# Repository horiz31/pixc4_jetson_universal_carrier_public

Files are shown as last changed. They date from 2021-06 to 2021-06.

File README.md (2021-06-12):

# PixC4 Jetson Universal Carrier Board Design Template
Schematic and Kicad board design for a PixC4-Jetson Universal Carrier Board

This project is intended to help users design a custom carrier board for the PixC4-Jetson. It contains a verified working design providing wide-input DC power regulation and typical connector pinouts.

A STEP file with 3D models is available here: https://drive.google.com/file/d/1p-Tw4490VoOuMsqg2tXlwOgqGBfQfWUK/view?usp=sharing

Designed in KiCad 5.1.8. KiCad is available for free download: https://www.kicad.org/download/

## Design Notes
#### Power
Power regulation is handled by two TI TPS54561QDPRRQ1 dc-dc converters. One is used to power the +5V bus, which is used to power the Nvidia Jetson. The other is used to power the +5V_FMU bus which is used to power the FMU. In general it is good design practice to separate the power system between that used for the Jetson and the FMU as we have done in this design. This way, even if an issue causes the Jetson bus to go into over-current protection, the core FMU may remain functional.

It is possible to implement a Power Selection Unit (PSU) for the FMU, providing even further redundancy. The ~VDD_POWERA_VALID and ~VDD_POWERB_VALID lines can be used in conjunction with a PSU to inform the FMU about the active power source. Note that the FMU USB port on the PixC4-Jetson can also power the FMU system, as this is useful for setup and downloading log files.

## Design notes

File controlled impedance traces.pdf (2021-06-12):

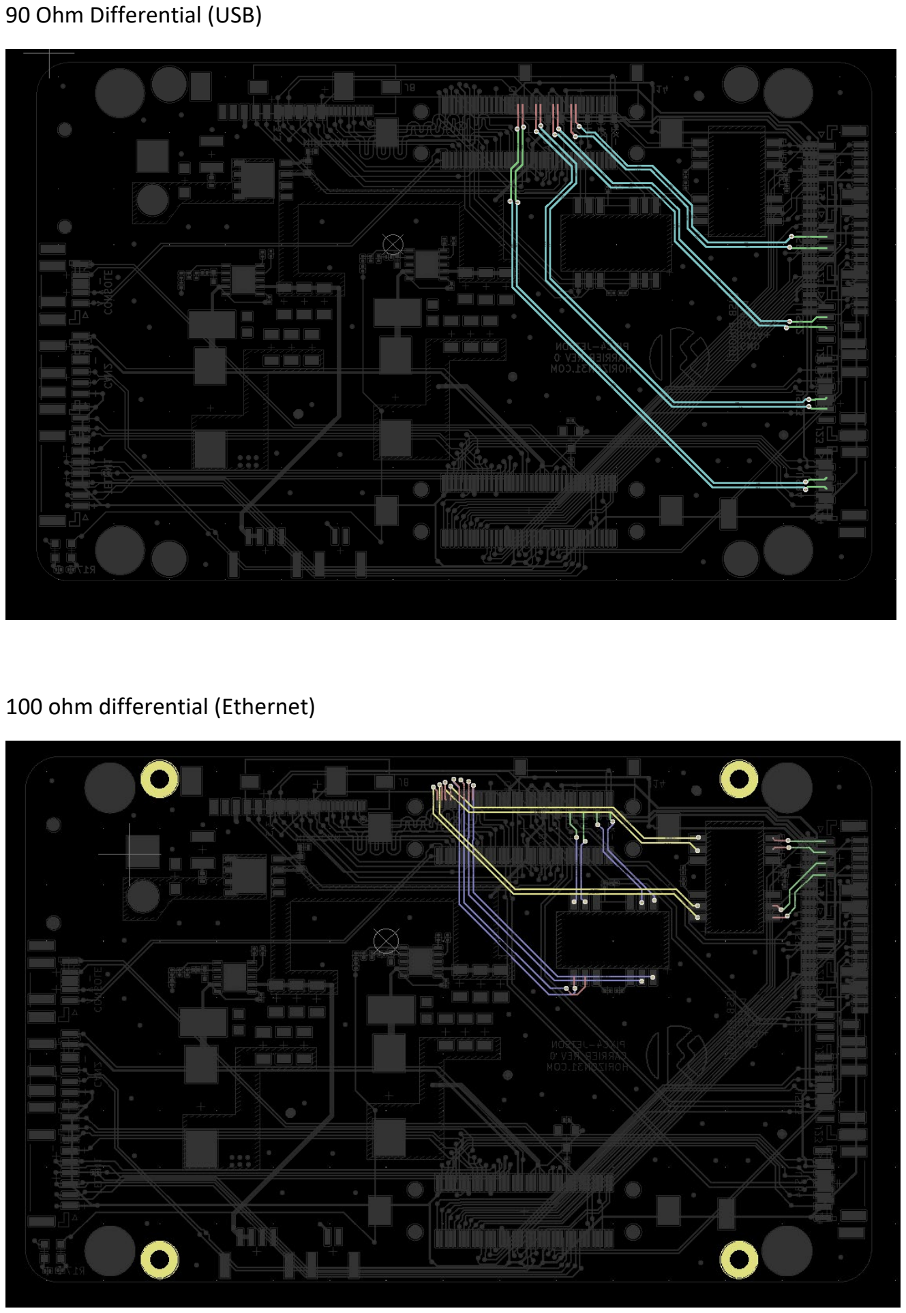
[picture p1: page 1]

90 Ohm Differential (USB)

100 ohm differential (Ethernet)

95 ohm differential (MIPI)

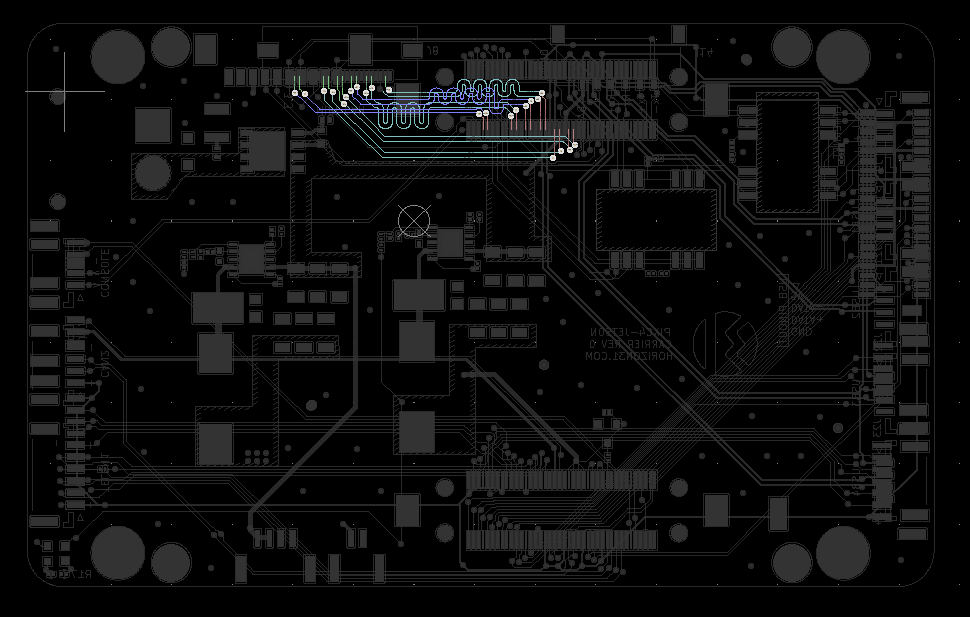
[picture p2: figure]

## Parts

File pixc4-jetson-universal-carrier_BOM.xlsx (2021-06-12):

PixC4-Jetson Universal Carrier Rev 1
Item | Qty | Reference(s) | Value | LibPart | Footprint | Part Num | Notes
1 | 6 | C1, C2, C3, C4, C20, C21 | 0.1uF | Device:C | Capacitors_SMD:C_0201 | GRM033R61E104KE14J
2 | 2 | C5, C6 | 1000pF | Device:C | Capacitors_SMD:C_0201 | GRM033R71H102KA12D
3 | 6 | C7, C8, C10, C11, C12, C13 | 2.2uF 100V | Device:C | Capacitors_SMD:C_1206 | 12061C225KAT2A
4 | 1 | C9 | 10uF 100V | Device:C | Capacitors_SMD:C_1210 | GRM32EC72A106KE05L
5 | 2 | C14, C15 | 10nF | Device:C | Capacitors_SMD:C_0201 | GRM033R71E103KE14D
6 | 2 | C16, C17 | 4.7nF | Device:C | Capacitors_SMD:C_0201 | GRM033R61E472KA12D
7 | 2 | C18, C19 | 47pF | Device:C | Capacitors_SMD:C_0402 | C0402C470J3RACAUTO
8 | 6 | C22, C23, C24, C25, C26, C27 | 47uF 10V | Device:C | Capacitors_SMD:C_1206 | CL31A476MPHNNNE
9 | 1 | D1 | TVS | osrf_device_fork:TVS | Diodes_SMD:D_SOD-123F | ATV02W101B-HF
10 | 2 | D2, D3 | PDS760-13 | Device:D_Schottky | UVDL:PDS760-13 | PDS760-13
11 | 2 | D4, D5 | LED_G | Device:LED | LEDs:LED_0603 | 150060VS75000
12 | 1 | D6 | D_Zener | Device:D_Zener | Diodes_SMD:D_SOD-523 | MM5Z12VT1G
13 | 6 | FID1, FID2, FID3, FID4, FID5, FID6 | Fiducial | Mechanical:Fiducial | Fiducials:Fiducial_0.5mm_Dia_1mm_Outer | DNI | DNI
14 | 4 | J1, J2, J3, J4 | Conn_01x01 | Connector_Generic:Conn_01x01 | Mounting_Holes:MountingHole_2.7mm_M2.5_Pad_Via | DNI | DNI
15 | 2 | J5, J6 | FX23L-80P-0.5SV10 | fx23l-80p-0.5sv8:FX23L-80P-0.5SV8 | UVDL:Hirose-FX23L-80P-0.5SV8-MFG | FX23L-80P-0.5SV10
16 | 3 | J7, J13, J16 | Conn_01x03 | Connector_Generic:Conn_01x03 | Connectors_JST:JST_GH_SM03B-GHS-TB_03x1.25mm_Angled | SM03B-GHS-TB(LF)(SN)
17 | 1 | J8 | Conn_01x22 | Connector_Generic:Conn_01x22 | UVDL:505110-2291 | 505110-2291
18 | 7 | J9, J12, J17, J21, J22, J23, J24 | Conn_01x04 | Connector_Generic:Conn_01x04 | Connectors_JST:JST_GH_SM04B-GHS-TB_04x1.25mm_Angled | SM04B-GHS-TB(LF)(SN)
19 | 1 | J10 | 532617010 | Connector_Generic:Conn_01x10 | Connectors_Molex:Molex_PicoBlade_53261-1071_10x1.25mm_Angled | 532617010
20 | 1 | J11 | Conn_01x02 | Connector_Generic:Conn_01x02 | Connectors_JST:JST_GH_SM02B-GHS-TB_02x1.25mm_Angled | SM02B-GHS-TB(LF)(SN)
21 | 1 | J14 | 504050-0691 | Connector_Generic:Conn_01x06 | UVDL:Molex-504050-0691-0-0-MFG | 504050-0691
22 | 1 | J15 | 5015714007 | Connector_Generic:Conn_02x20_Odd_Even | UVDL:5015714007 | 5015714007
23 | 1 | J18 | Conn_01x06 | Connector_Generic:Conn_01x06 | Connectors_JST:JST_GH_SM06B-GHS-TB_06x1.25mm_Angled | SM06B-GHS-TB(LF)(SN)
24 | 1 | J19 | Conn_01x05 | Connector_Generic:Conn_01x05 | Connectors_JST:JST_GH_SM05B-GHS-TB_05x1.25mm_Angled | SM05B-GHS-TB(LF)(SN)
25 | 1 | J20 | Conn_01x10 | Connector_Generic:Conn_01x10 | Connectors_JST:JST_GH_SM10B-GHS-TB_10x1.25mm_Angled | SM10B-GHS-TB(LF)(SN)
26 | 1 | J25 | Conn_01x07 | Connector_Generic:Conn_01x07 | Connectors_JST:JST_GH_SM07B-GHS-TB_07x1.25mm_Angled | SM07B-GHS-TB(LF)(SN)
27 | 1 | J27 | XT30PW-M | Connector_Generic:Conn_01x02 | UVDL:AMASS_XT30PW-M_1x02_P2.50mm_Horizontal | XT30PW-M
28 | 2 | L1, L2 | ASPIAIG-F1040-7R3M-T | Device:L | UVDL:ASPIAIG-F1040-7R3M-T | ASPIAIG-F1040-7R3M-T
29 | 1 | Q1 | Q_NMOS_GSD | Device:Q_NMOS_GSD | TO_SOT_Packages_SMD:SOT-23 | BSS214NH6327XTSA1
30 | 1 | Q2 | FDWS9508L | archangel:FDWS9508L | patrios:TRANS_FDMS0300S | FDWS9508L-F085
31 | 1 | R1 | 10K | Device:R | Resistors_SMD:R_0201 | ERJ-1GNF1002C
32 | 1 | R2 | 220 | Device:R | Resistors_SMD:R_0201 | ERJ-1GNF2200C
33 | 2 | R3, R4 | 75 | Device:R | Resistors_SMD:R_0201 | ERJ-1GNF75R0C
34 | 1 | R5 | 750m | Device:R | Resistors_SMD:R_0402 | ERJ-2BQJR75X
35 | 2 | R6, R7 | 16.9K | Device:R | Resistors_SMD:R_0201 | ERJ-1GNF1692C
36 | 2 | R8, R9 | 243K | Device:R | Resistors_SMD:R_0201 | ERJ-1GNF2433C
37 | 2 | R10, R13 | 49.9 | Device:R | Resistors_SMD:R_0201 | ERJ-1GEF49R9C
38 | 2 | R11, R14 | 53.6K | Device:R | Resistors_SMD:R_0201 | ERJ-1GNF5362C
39 | 2 | R12, R15 | 10.2K | Device:R | Resistors_SMD:R_0201 | ERJ-1GNF1022C
40 | 2 | R16, R17 | 1.0K | Device:R | Resistors_SMD:R_0201 | ERJ-1GEF1001C
41 | 1 | R18 | 10K | Device:R | Resistors_SMD:R_0402 | ERJ-PA2J103X
42 | 1 | R19 | 100 | Device:R | Resistors_SMD:R_0201 | ERJ-U01F1000C
43 | 2 | U1, U2 | HX0068ANLT | Microhard:HX0068ANLT | Nightcrawler:HX0068ANLT_r2 | HX0068ANLT
44 | 2 | U3, U4 | TPS54561QDPRRQ1 | TPS54561DPRR:TPS54561DPRR | UVDL:SON80P400X400X80-11N | TPS54561QDPRRQ1
45 | 1 | U5 | DoodleSmart | archangel:DoodleSmart | Nightcrawler:Doodle | DNI

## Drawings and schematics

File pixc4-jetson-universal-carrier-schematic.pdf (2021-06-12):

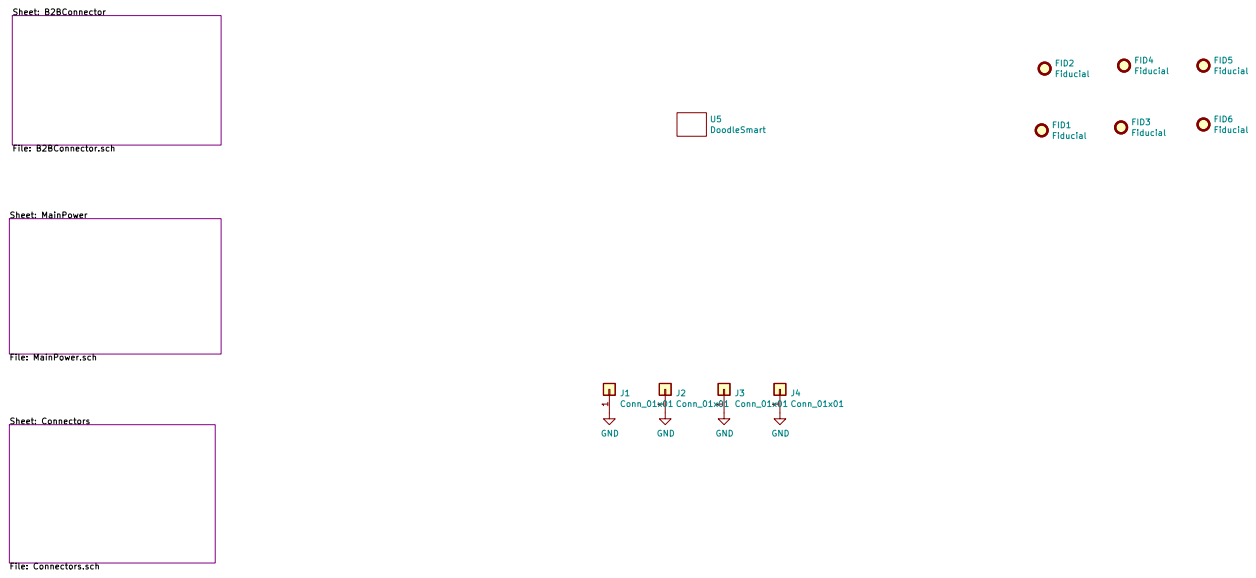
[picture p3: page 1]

Sheet: Connectors File: Connectors.sch

File: pixc4-jetson-universal-carrier.sch Sheet: / Horizon31.com

Id: 1/4 Title: PixC4-Jetson Universal Carrier

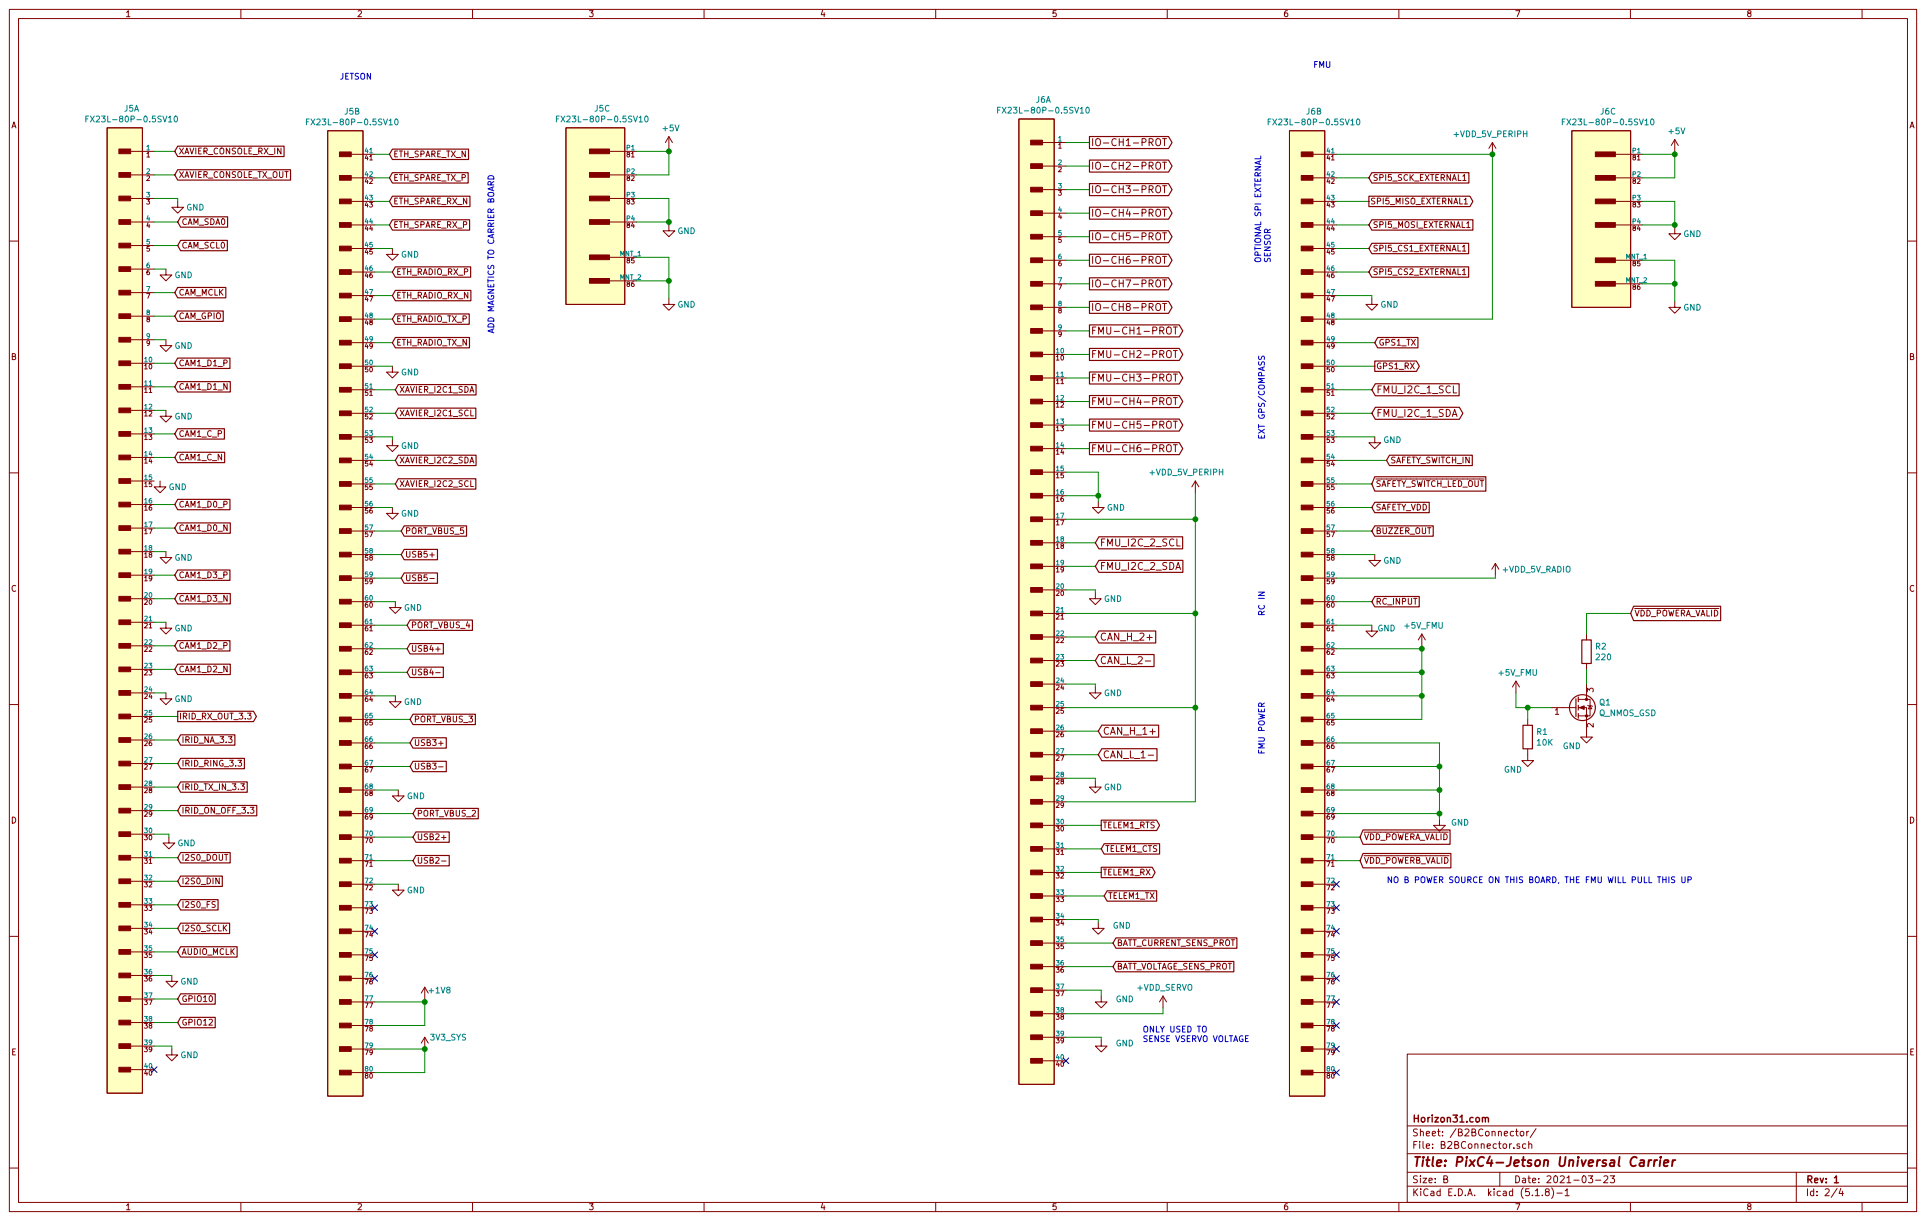
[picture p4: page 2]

GND GND GND GND GND GND GND

Id: 2/4 Title: PixC4-Jetson Universal Carrier File: B2BConnector.sch Sheet: /B2BConnector/ Horizon31.com

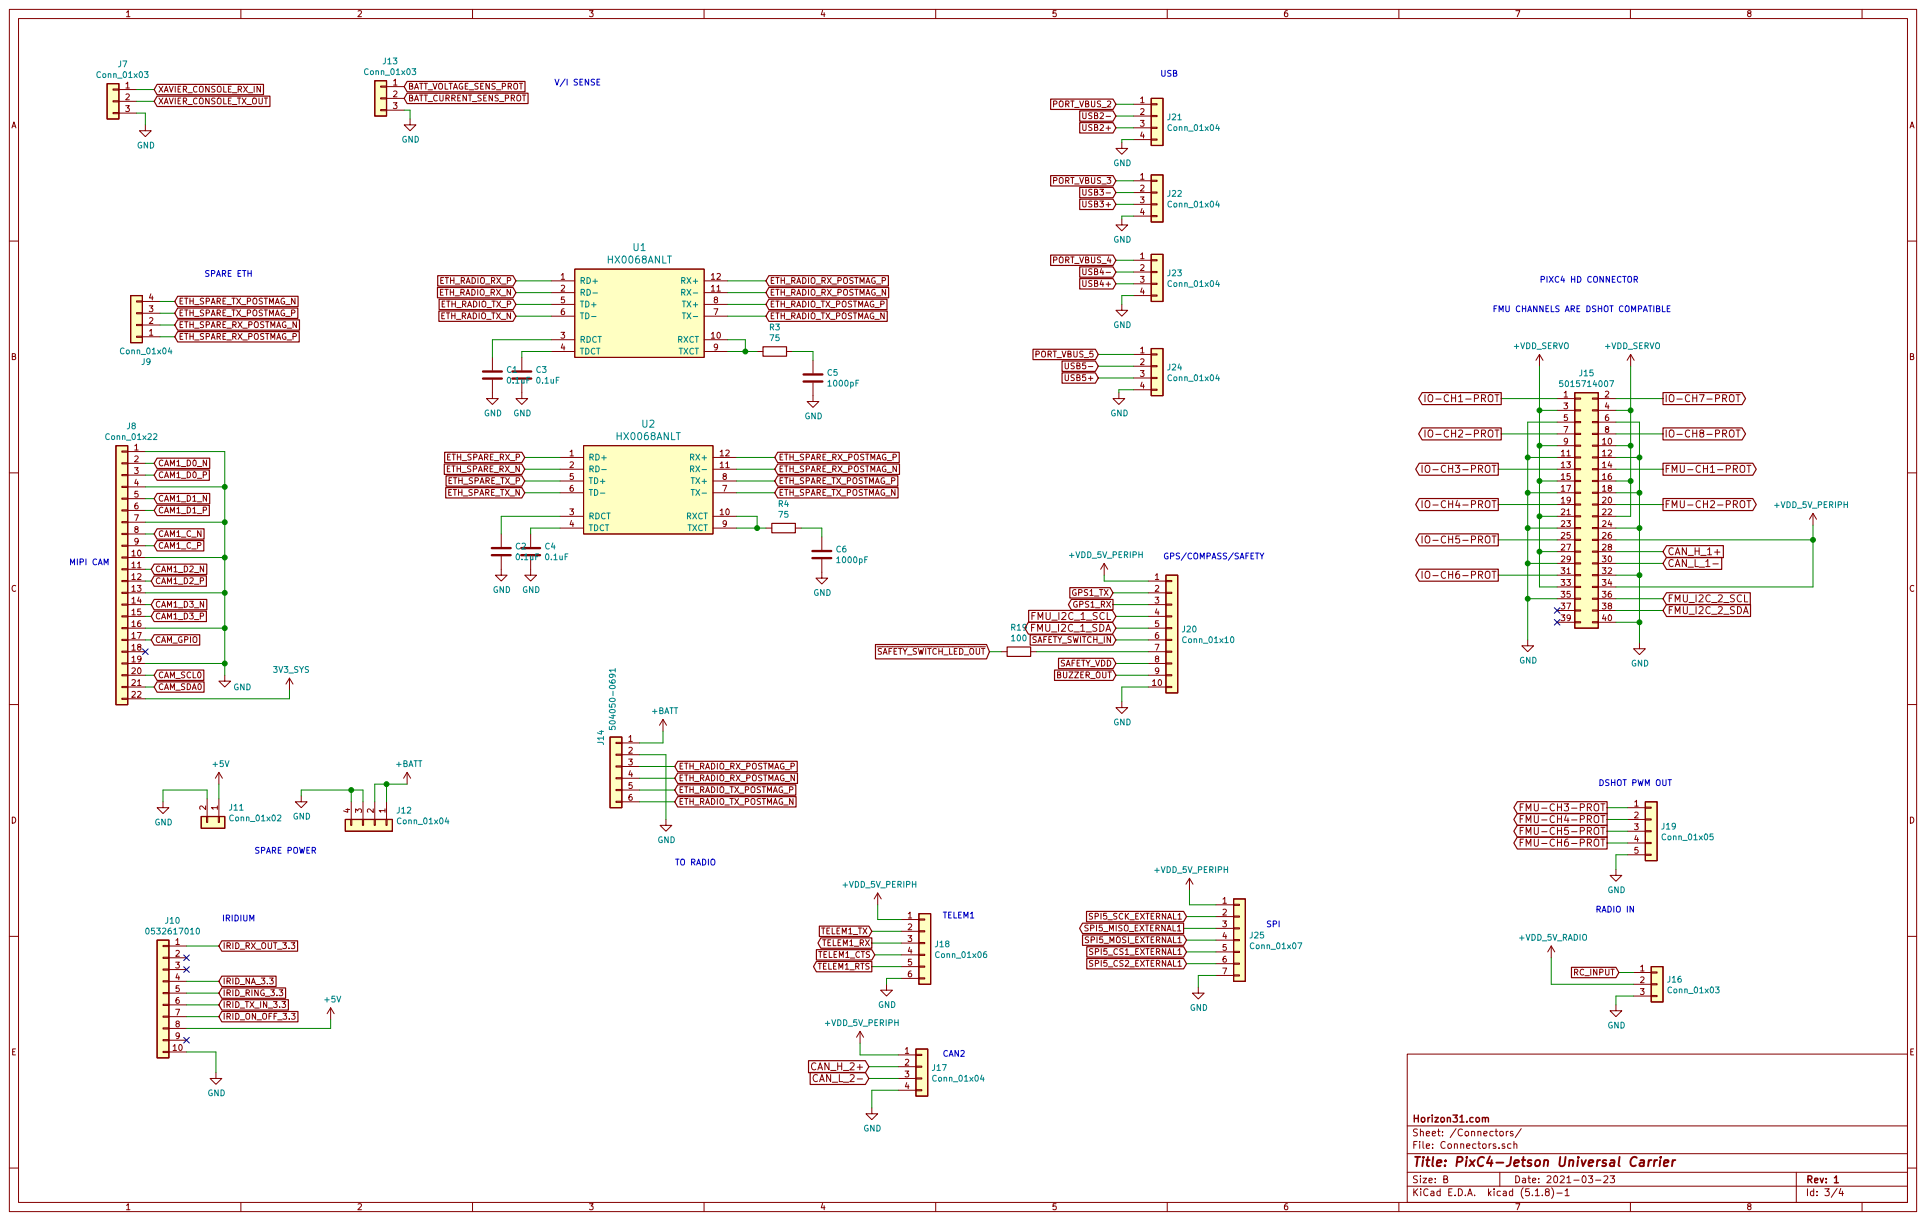
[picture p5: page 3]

FMU CHANNELS ARE DSHOT COMPATIBLE

9 | | 10
11 | | 12
13 | | 14
15 | | 16
17 | | 18
19 | | 20
21 | | 22
23 | | 24
25 | | 26
27 | | 28
29 | | 30
31 | | 32
33 | | 34

SPARE POWER MIPI CAM

Id: 3/4 Title: PixC4-Jetson Universal Carrier File: Connectors.sch Sheet: /Connectors/ Horizon31.com

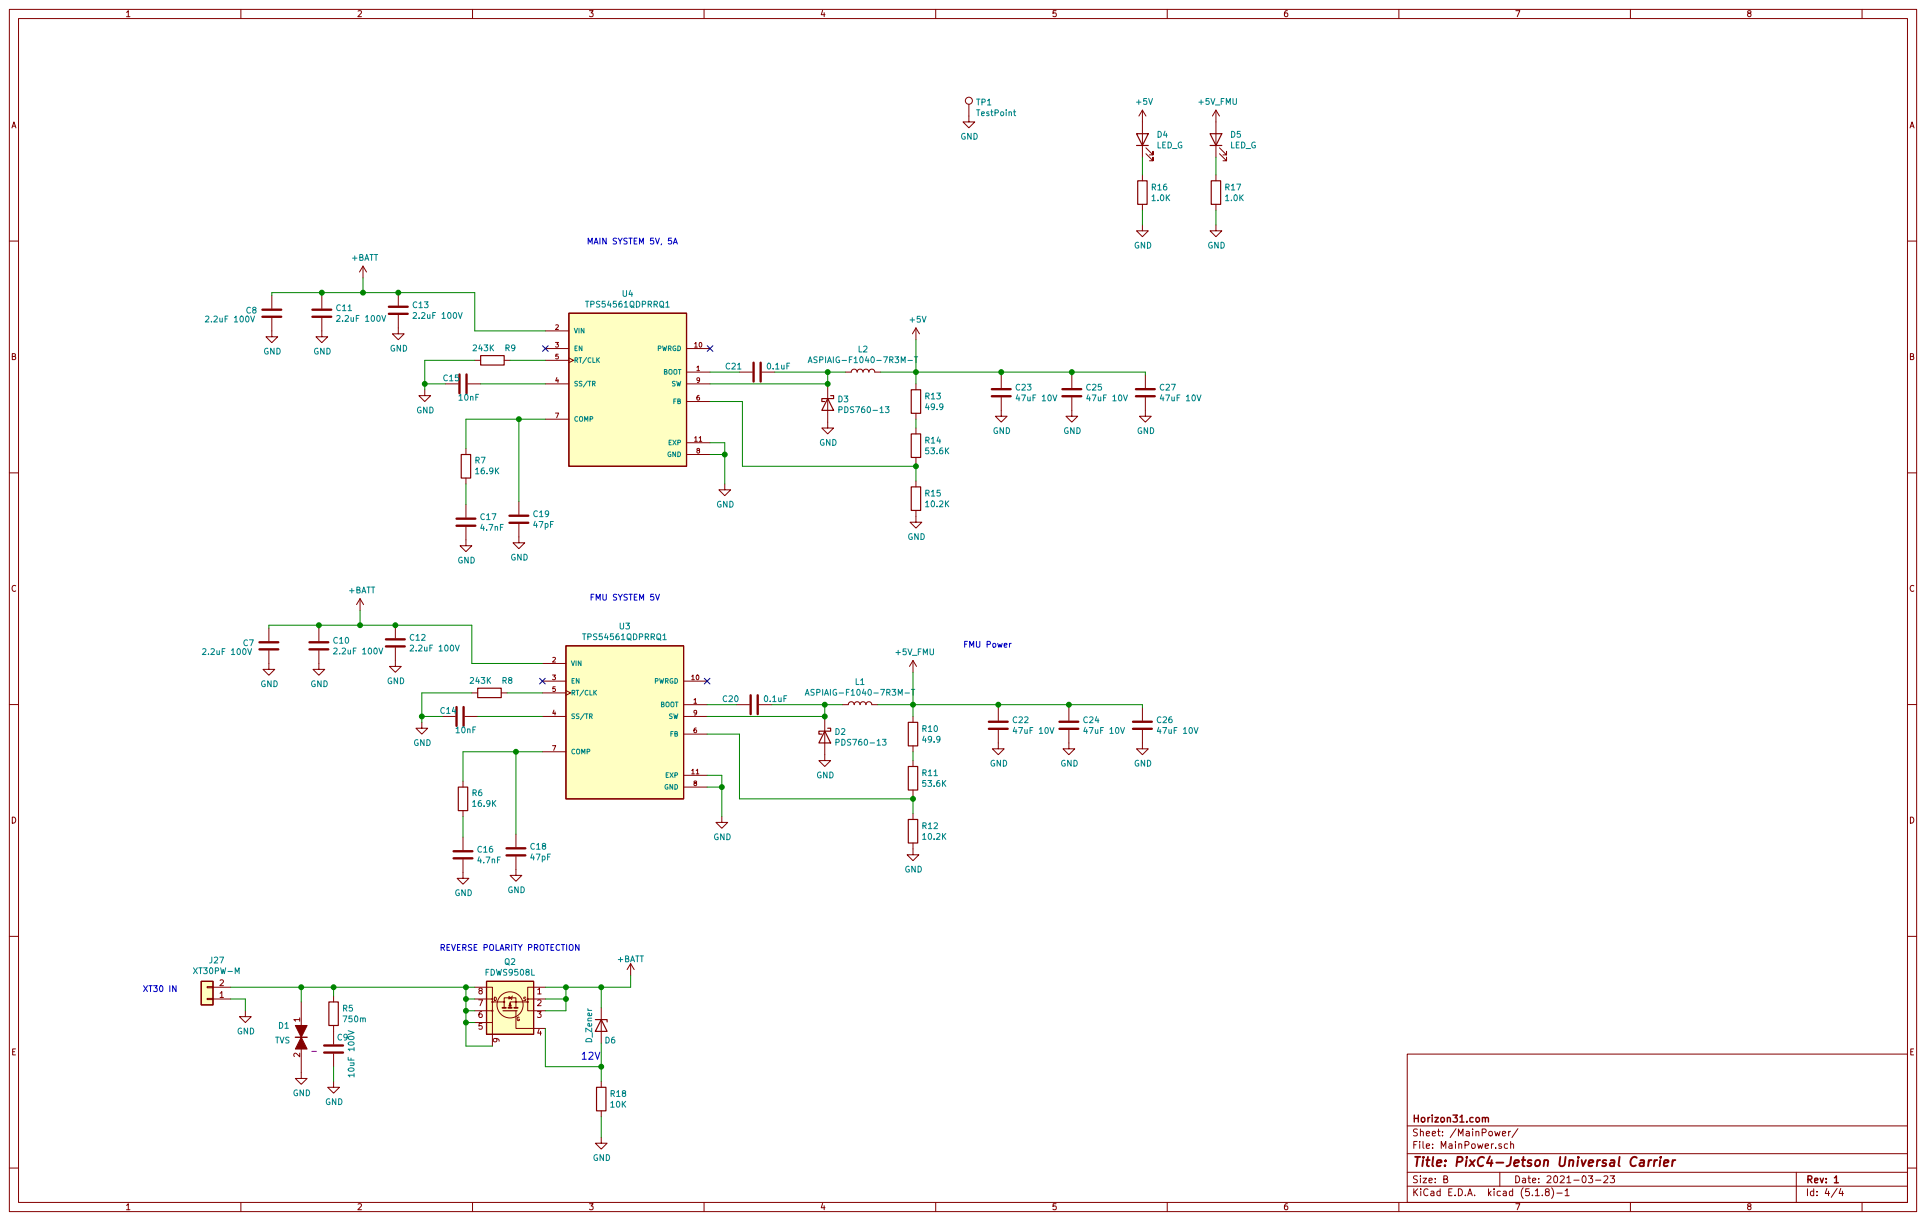
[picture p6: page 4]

Id: 4/4 Title: PixC4-Jetson Universal Carrier File: MainPower.sch Sheet: /MainPower/ Horizon31.com

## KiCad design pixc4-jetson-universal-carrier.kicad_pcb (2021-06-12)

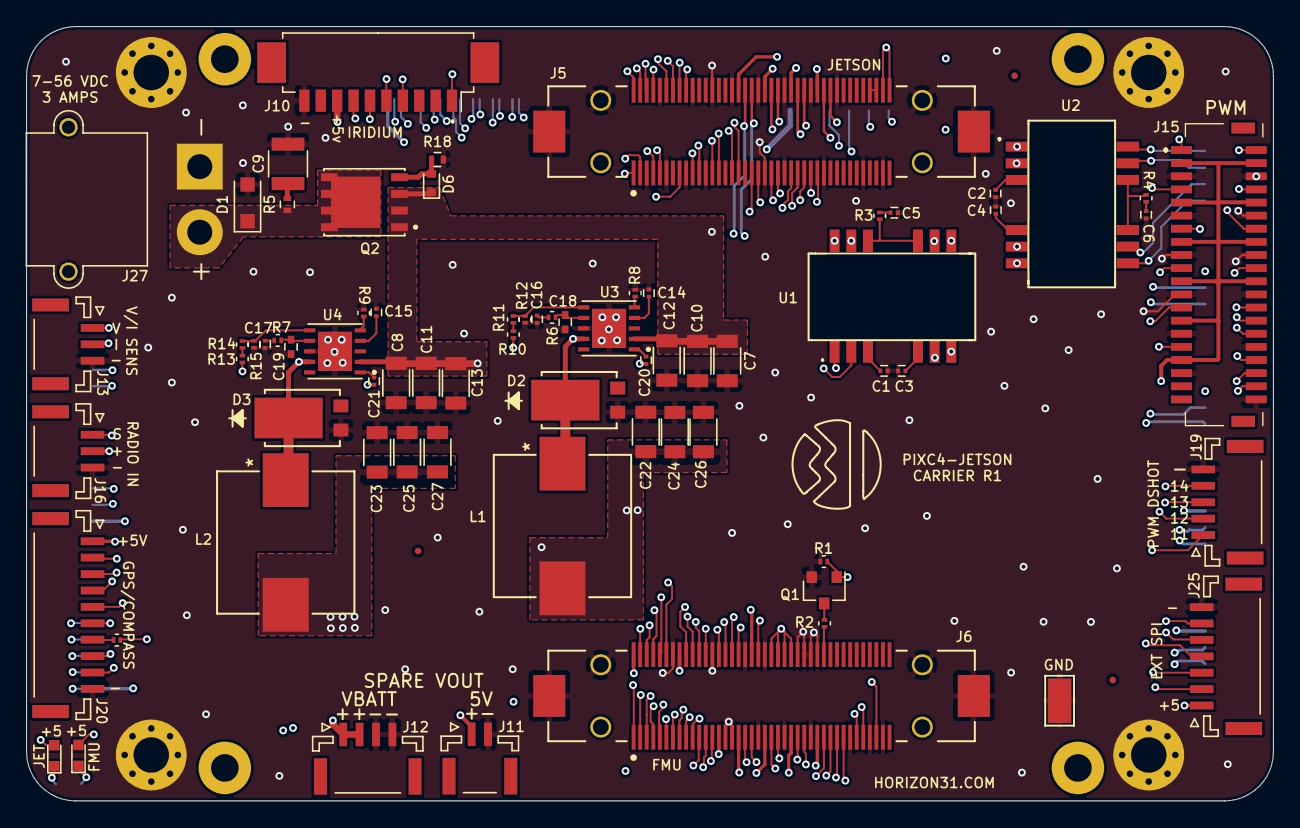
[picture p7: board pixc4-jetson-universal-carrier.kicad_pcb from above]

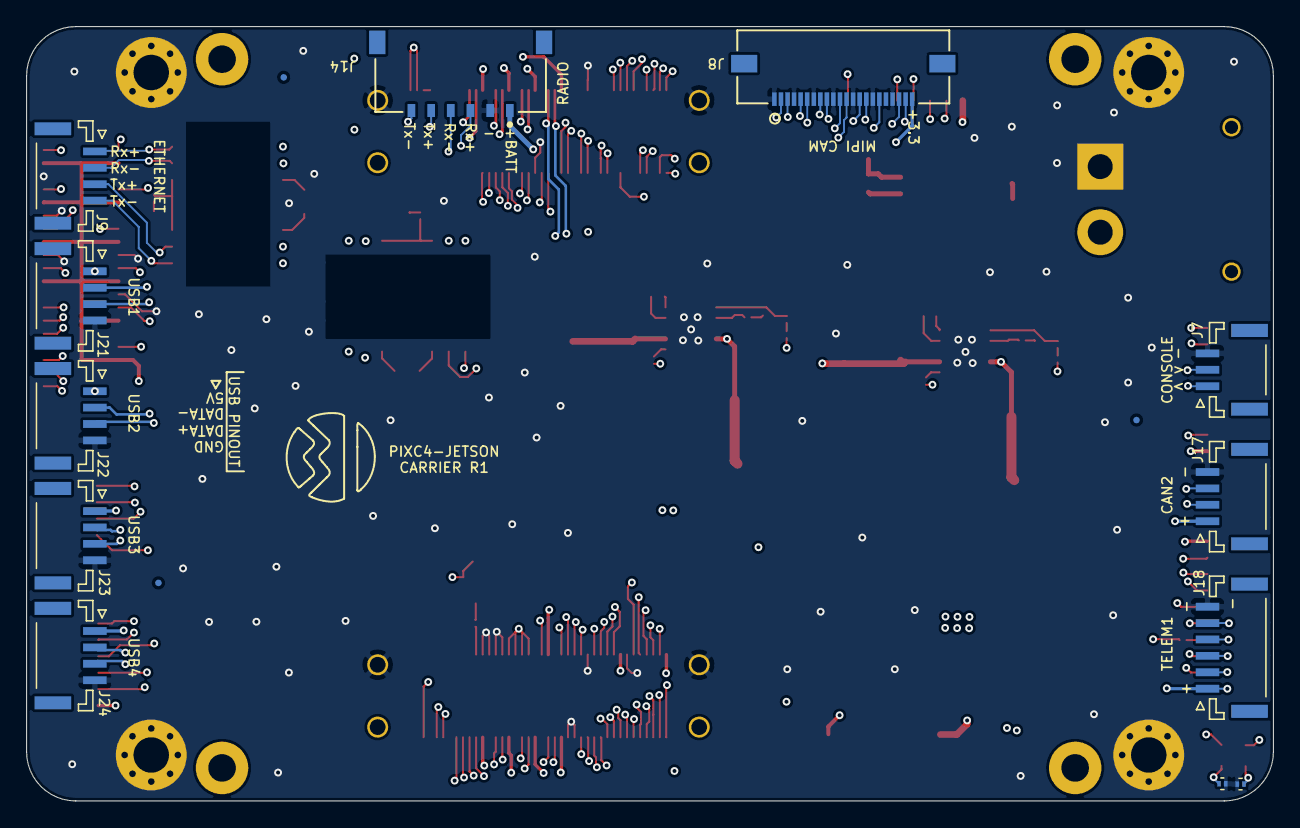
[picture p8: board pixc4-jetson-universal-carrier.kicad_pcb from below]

Board: 8 copper layers, 95.0 x 59.0 mm, 94 parts (15 on the bottom side), 129 nets.

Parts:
C1, C2, C3, C4, C20, C21: 0.1uF; C_0201
C5, C6: 1000pF; C_0201
C7, C8, C10, C11, C12, C13: 2.2uF 100V; C_1206
C9: 10uF 100V; C_1210
C14, C15: 10nF; C_0201
C16, C17: 4.7nF; C_0201
C18, C19: 47pF; C_0402
C22, C23, C24, C25, C26, C27: 47uF 10V; C_1206
D1: TVS; D_SOD-123F
D2, D3: PDS760-13
D4, D5: LED_G; LED_0603
D6: D_Zener; D_SOD-523
FID1, FID2, FID3, FID4, FID5, FID6: Fiducial; Fiducial_0.5mm_Dia_1mm_Outer
J1, J2, J3, J4: Conn_01x01; MountingHole_2.7mm_M2.5_Pad_Via
J5, J6: FX23L-80P-0.5SV10; Hirose-FX23L-80P-0.5SV8-MFG
J7, J13, J16: Conn_01x03; JST_GH_SM03B-GHS-TB_03x1.25mm_Angled
J8: Conn_01x22; 505110-2291
J9, J12, J17, J21, J22, J23, J24: Conn_01x04; JST_GH_SM04B-GHS-TB_04x1.25mm_Angled
J10: 0532617010; Molex_PicoBlade_53261-1071_10x1.25mm_Angled
J11: Conn_01x02; JST_GH_SM02B-GHS-TB_02x1.25mm_Angled
J14: 504050-0691; Molex-504050-0691-0-0-MFG
J15: 5015714007
J18: Conn_01x06; JST_GH_SM06B-GHS-TB_06x1.25mm_Angled
J19: Conn_01x05; JST_GH_SM05B-GHS-TB_05x1.25mm_Angled
J20: Conn_01x10; JST_GH_SM10B-GHS-TB_10x1.25mm_Angled
J25: Conn_01x07; JST_GH_SM07B-GHS-TB_07x1.25mm_Angled
J27: XT30PW-M; AMASS_XT30PW-M_1x02_P2.50mm_Horizontal
L1, L2: ASPIAIG-F1040-7R3M-T
Q1: Q_NMOS_GSD; SOT-23
Q2: FDWS9508L; TRANS_FDMS0300S
R1: 10K; R_0201
R2: 220; R_0201
R3, R4: 75; R_0201
R5: 750m; R_0402
R6, R7: 16.9K; R_0201
R8, R9: 243K; R_0201
R10, R13: 49.9; R_0201
R11, R14: 53.6K; R_0201
R12, R15: 10.2K; R_0201
R16, R17: 1.0K; R_0201
R18: 10K; R_0402
R19: 100; R_0201
TP1: TestPoint; Test_Point_Keystone_5015_Micro-Minature
U1, U2: HX0068ANLT; HX0068ANLT_r2
U3, U4: TPS54561QDPRRQ1; SON80P400X400X80-11N
U5: DoodleSmart; Doodle

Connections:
3V3_SYS: J5.79, J5.80, J8.22
+1V8: J5.77, J5.78
+5V: C23.1, C25.1, C27.1, D4.2, J5.81, J5.82, J6.81, J6.82, J10.8, J11.1, L2.2, R13.1
+5V_FMU: C22.1, C24.1, C26.1, D5.2, J6.62, J6.63, J6.64, J6.65, L1.2, Q1.1, R1.1, R10.1
+BATT: C7.1, C8.1, C10.1, C11.1, C12.1, C13.1, D6.1, J12.1, J12.2, J14.1, Q2.1, Q2.2, Q2.3, U3.2, U4.2
+VDD_5V_PERIPH: J6.17, J6.21, J6.25, J6.29, J6.41, J6.48, J15.26, J15.34, J17.1, J18.1, J20.1, J25.1
+VDD_5V_RADIO: J6.59, J16.2
+VDD_SERVO: J6.38, J15.3, J15.4, J15.9, J15.10, J15.15, J15.16, J15.21, J15.22, J15.27, J15.33
BATT_CURRENT_SENS_PROT: J6.35, J13.2
BATT_VOLTAGE_SENS_PROT: J6.36, J13.1
BUZZER_OUT: J6.57, J20.9
CAM1_C_N: J5.14, J8.8
CAM1_C_P: J5.13, J8.9
CAM1_D0_N: J5.17, J8.2
CAM1_D0_P: J5.16, J8.3
CAM1_D1_N: J5.11, J8.5
CAM1_D1_P: J5.10, J8.6
CAM1_D2_N: J5.23, J8.11
CAM1_D2_P: J5.22, J8.12
CAM1_D3_N: J5.20, J8.14
CAM1_D3_P: J5.19, J8.15
CAM_GPIO: J5.8, J8.17
CAM_SCL0: J5.5, J8.20
CAM_SDA0: J5.4, J8.21
CAN_H_1+: J6.26, J15.28
CAN_H_2+: J6.22, J17.2
CAN_L_1-: J6.27, J15.30
CAN_L_2-: J6.23, J17.3
ETH_RADIO_RX_N: J5.47, U1.2
ETH_RADIO_RX_P: J5.46, U1.1
ETH_RADIO_RX_POSTMAG_N: J14.4, U1.11
ETH_RADIO_RX_POSTMAG_P: J14.3, U1.12
ETH_RADIO_TX_N: J5.49, U1.6
ETH_RADIO_TX_P: J5.48, U1.5
ETH_RADIO_TX_POSTMAG_N: J14.6, U1.7
ETH_RADIO_TX_POSTMAG_P: J14.5, U1.8
ETH_SPARE_RX_N: J5.43, U2.2
ETH_SPARE_RX_P: J5.44, U2.1
ETH_SPARE_RX_POSTMAG_N: J9.2, U2.11
ETH_SPARE_RX_POSTMAG_P: J9.1, U2.12
ETH_SPARE_TX_N: J5.41, U2.6
ETH_SPARE_TX_P: J5.42, U2.5
ETH_SPARE_TX_POSTMAG_N: J9.4, U2.7
ETH_SPARE_TX_POSTMAG_P: J9.3, U2.8
FMU-CH1-PROT: J6.9, J15.14
FMU-CH2-PROT: J6.10, J15.20
FMU-CH3-PROT: J6.11, J19.1
FMU-CH4-PROT: J6.12, J19.2
FMU-CH5-PROT: J6.13, J19.3
FMU-CH6-PROT: J6.14, J19.4
FMU_I2C_1_SCL: J6.51, J20.4
FMU_I2C_1_SDA: J6.52, J20.5
FMU_I2C_2_SCL: J6.18, J15.36
FMU_I2C_2_SDA: J6.19, J15.38
GND: C1.2, C2.2, C3.2, C4.2, C5.2, C6.2, C7.2, C8.2, C9.2, C10.2, C11.2, C12.2, C13.2, C14.2, C15.2, C16.2, C17.2, C18.2, C19.2, C22.2, C23.2, C24.2, C25.2, C26.2, C27.2, D1.2, D2.2, D3.2, J1.1, J2.1, J3.1, J4.1, J5.3, J5.6, J5.9, J5.12, J5.18, J5.21, J5.24, J5.30, J5.36, J5.39, J5.45, J5.50, J5.53, J5.56, J5.60, J5.64, J5.68, J5.72, J5.83, J5.84, J5.85, J5.86, J6.15, J6.16, J6.20, J6.24, J6.28, J6.34, J6.37, J6.39, J6.47, J6.53, J6.58, J6.61, J6.66, J6.67, J6.68, J6.69, J6.83, J6.84, J6.85, J6.86, J7.3, J8.1, J8.4, J8.7, J8.10, J8.13, J8.16, J8.19, J10.10, J11.2, J12.3, J12.4, J13.3, J14.2, J15.5, J15.6, J15.11, J15.12, J15.17, J15.18, J15.23, J15.24, J15.29, J15.32, J15.35, J15.40, J16.3, J17.4, J18.6, J19.5, J20.10, J21.4, J22.4, J23.4, J24.4, J25.7, J27.1, Q1.2, R1.2, R8.1, R9.1, R12.2, R15.2, R16.2, R17.2, R18.2, TP1.1, U3.8, U3.11, U4.8, U4.11
GPS1_RX: J6.50, J20.3
GPS1_TX: J6.49, J20.2
IO-CH1-PROT: J6.1, J15.1
IO-CH2-PROT: J6.2, J15.7
IO-CH3-PROT: J6.3, J15.13
IO-CH4-PROT: J6.4, J15.19
IO-CH5-PROT: J6.5, J15.25
IO-CH6-PROT: J6.6, J15.31
IO-CH7-PROT: J6.7, J15.2
IO-CH8-PROT: J6.8, J15.8
IRID_NA_3.3: J5.26, J10.4
IRID_ON_OFF_3.3: J5.29, J10.7
IRID_RING_3.3: J5.27, J10.5
IRID_RX_OUT_3.3: J5.25, J10.1
IRID_TX_IN_3.3: J5.28, J10.6
unnamed: C1.1, U1.3
unnamed: C2.1, U2.3
unnamed: C3.1, U1.4
unnamed: C4.1, U2.4
unnamed: C5.1, R3.1
unnamed: C6.1, R4.1
unnamed: C9.1, R5.2
unnamed: C14.1, U3.4
unnamed: C15.1, U4.4
unnamed: C16.1, R6.1
unnamed: C17.1, R7.1
unnamed: C18.1, R6.2, U3.7
unnamed: C19.1, R7.2, U4.7
unnamed: C20.1, D2.1, L1.1, U3.9
unnamed: C20.2, U3.1
unnamed: C21.1, D3.1, L2.1, U4.9
unnamed: C21.2, U4.1
unnamed: D1.1, J27.2, Q2.5, Q2.6, Q2.7, Q2.8, Q2.9, R5.1
unnamed: D4.1, R16.1
unnamed: D5.1, R17.1
unnamed: D6.2, Q2.4, R18.1
unnamed: J20.7, R19.1
unnamed: Q1.3, R2.2
unnamed: R3.2, U1.9, U1.10
unnamed: R4.2, U2.9, U2.10
unnamed: R8.2, U3.5
unnamed: R9.2, U4.5
unnamed: R10.2, R11.1
unnamed: R11.2, R12.1, U3.6
unnamed: R13.2, R14.1
unnamed: R14.2, R15.1, U4.6
PORT_VBUS_2: J5.69, J21.1
PORT_VBUS_3: J5.65, J22.1
PORT_VBUS_4: J5.61, J23.1
PORT_VBUS_5: J5.57, J24.1
RC_INPUT: J6.60, J16.1
SAFETY_SWITCH_IN: J6.54, J20.6
SAFETY_VDD: J6.56, J20.8
SPI5_CS1_EXTERNAL1: J6.45, J25.5
SPI5_CS2_EXTERNAL1: J6.46, J25.6
SPI5_MISO_EXTERNAL1: J6.43, J25.3
SPI5_MOSI_EXTERNAL1: J6.44, J25.4
SPI5_SCK_EXTERNAL1: J6.42, J25.2
TELEM1_CTS: J6.31, J18.4
TELEM1_RTS: J6.30, J18.5
TELEM1_RX: J6.32, J18.3
TELEM1_TX: J6.33, J18.2
USB2+: J5.70, J21.3
USB2-: J5.71, J21.2
USB3+: J5.66, J22.3
USB3-: J5.67, J22.2
USB4+: J5.62, J23.3
USB4-: J5.63, J23.2
USB5+: J5.58, J24.3
USB5-: J5.59, J24.2
XAVIER_CONSOLE_RX_IN: J5.1, J7.1
XAVIER_CONSOLE_TX_OUT: J5.2, J7.2
~SAFETY_SWITCH_LED_OUT: J6.55, R19.2
~VDD_POWERA_VALID: J6.70, R2.1
